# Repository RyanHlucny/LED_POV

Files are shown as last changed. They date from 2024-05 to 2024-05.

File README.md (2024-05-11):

# LED_POV

[NDSU](https://www.ndsu.edu/) Senior Design project: Two foot diameter LED spinning display using persistence-of-vision techniques.

## Documentation

The Documentation for this project is done using [GitHub Flavored Markdown (GFM)](https://github.github.com/gfm/) and [GitHub Pages](https://pages.github.com/). You can navigate around using the headers on the website. Many items are linked together, making for especially easy navigation.

## Software Development

If you are interested in setting up your software development environment similar to how I did in this project, I wrote a 'getting started' page for this. You can find that page at [Software Development](https://github.com/RyanHlucny/LED_POV/blob/main/SD403/Ryan%20Hlucny/Software%20Development/GettingStarted.md)

## Weekly Meetings

Our weekly meetings were where we got a lot of stuff done, and we took a lot of care and effort to document as much of the build process as we could. So please check out [Weekly Meetings](https://github.com/RyanHlucny/LED_POV/blob/main/SD403/Weekly%20Meetings/Weekly_Meetings.md) to see and learn more about this project.

## Media

Photos and videos from the project have been added to this [Google Photos Album](https://photos.app.goo.gl/s6BoLq5Lydn7EBvv7).

## THANK YOU

Got questions? [Contact us](https://github.com/RyanHlucny/LED_POV/blob/main/SD403/HW01/HW01_Contact_Information.md).

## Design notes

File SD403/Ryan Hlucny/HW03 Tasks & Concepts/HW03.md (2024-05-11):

# HW03 - Tasks & Concepts

## Ryan Hlucny

### Overview

- [Project Role](#project-role)
- [Tasks](#tasks)
- [Gantt Chart](#gantt-chart)
- [ECE Concepts](#ece-concepts)
- [ECE Tools](#ece-tools)

---

### Project Role

My role on the project is the Software and Controls lead. I will be overseeing the design of the software and controls for the project.

---

### Tasks

#### Task 1 - Image Transform & Processing

- Image pre-processing
- Pixel Transformation
- Brightness compensation
- Lag Compensation (to prevent "swirl" effect)
- ECE Concept: Image processing, Matlab

#### Task 2 - LED Control

- LED driver routine
- High-speed SPI communications
- ECE Concept: Embedded LED control

#### Task 3 - Interrupts

- Updating the LED command
- Reading sensor values
- ECE Concept: Embedded MCU Interrupts

#### Task 4 - State Space Model and Observer

- State Space model of system
- Observer design
- Angle estimation
- Latency Compensation?
- ECE Concept: Modern Control State Space modeling and Observing

---

### Gantt Chart

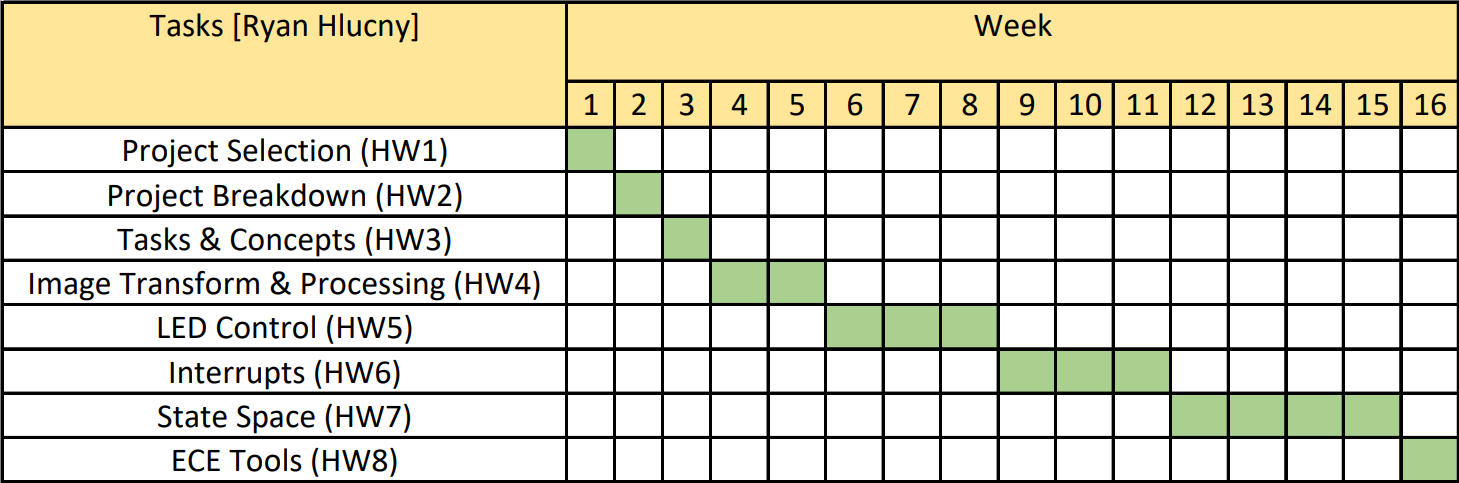
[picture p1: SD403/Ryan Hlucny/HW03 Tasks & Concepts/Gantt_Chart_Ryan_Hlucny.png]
Gantt Chart


---

### ECE Concepts

As listed in each of the above Tasks, my concepts are

- Concept 1 - Image Processing, Matlab
- Concept 2 - Embedded LED Control
- Concept 3 - Embedded MCU Interrupts
- Concept 4 - Modern Control State Space modeling and Observing

---

### ECE Tools

**Oscilloscope** - Measuring signal timing and signal characteristics. Debugging SPI communication channel between [Raspberry Pi Pico W](https://www.raspberrypi.com/documentation/microcontrollers/raspberry-pi-pico.html) and custom LED board utilizing [Adafruit DotStar (SK9822) Addressable RGB LEDs](https://www.adafruit.com/product/2343), and I2C Communications to [IMU sensor](https://www.sparkfun.com/products/15335).

**Development Environments** - I will be using [VS Code](https://code.visualstudio.com/) and the [Platform.io extension](https://platformio.org/) to develop the embedded code for the [Raspberry Pi Pico W](https://www.raspberrypi.com/documentation/microcontrollers/raspberry-pi-pico.html) in C++. I am running an [arduino-pico core](https://arduino-pico.readthedocs.io/en/latest/index.html), which ports the RP2040 mcu to the Arduino ecosystem, from [earlephilhower](https://github.com/earlephilhower/arduino-pico). The documentation for arduino-pico can be found [here](https://arduino-pico.readthedocs.io/en/latest/index.html).

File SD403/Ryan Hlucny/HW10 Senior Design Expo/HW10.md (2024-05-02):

# HW10 - Senior Design Expo

## Ryan Hlucny

### Favorite Project

My favorite project from the Senior Design Expo is the Head Tracker camera on the articulating/rotating platform using an IMU. I liked that it was interactive and it followed the sensor's movements really well. There were a lot of aspects to this project. Including wireless connectivity and a visualizer application. The ESP32 camera was also really cool! I could see uses for this in a deployable military/disaster recovery robot as a way for the operator to be able to clearly see around the robot while remotely controlling it. Very cool!

### Improvement

To improve the presentation, I would probably display a cut-section view of the rotation device to show off the internals and some diagrams to show the overview of the design. I would also like to see some kind of head/helmet mount for the sensor and have it battery powered so it doesn't have to be plugged in.

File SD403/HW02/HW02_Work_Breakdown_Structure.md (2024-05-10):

# Work Breakdown Structure - LED_POV

## SD_403_Sp24_06 LED Spinner

```mermaid
flowchart TB
  subgraph one [ ]
    L1(Level 1)
    A("
    Project 
    LED Spinning Display
    ")
  end
  subgraph two [ ]
    L2(Level 2)
    A --> B1("
    Ryan Hlucny
    Software/Controls
    ")
    A --> B2("
    Austin Houle
    Power Electronics
    ")
    A --> B3("
    Austin Kallhoff
    Mechanical/Hardware
    ")
  end
  subgraph three [ ]
    L3(Level 3)
    B1 --> C1(Major Activity)
    B1 --> C2(Major Activity)
    B2 --> C3(Major Activity)
    B2 --> C4(Major Activity)
    B3 --> C5(Major Activity)
    B3 --> C6(Major Activity)
  end
  subgraph four [ ]
    L4(Level 4)
    C1 --> T1(Task 1)
    C1 --> T2(Task 2)
    C2 --> T3(Task 3)
    C2 --> T4(Task 4)
    C3 --> T5(Task 1)
    C3 --> T6(Task 2)
    C4 --> T7(Task 3)
    C4 --> T8(Task 4)
    C5 --> T9(Task 1)
    C5 --> T10(Task 2)
    C6 --> T11(Task 3)
    C6 --> T12(Task 4)
  end
```

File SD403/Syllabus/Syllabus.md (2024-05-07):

# SD403 Syllabus

## SD_403_Sp24_06 LED Spinner

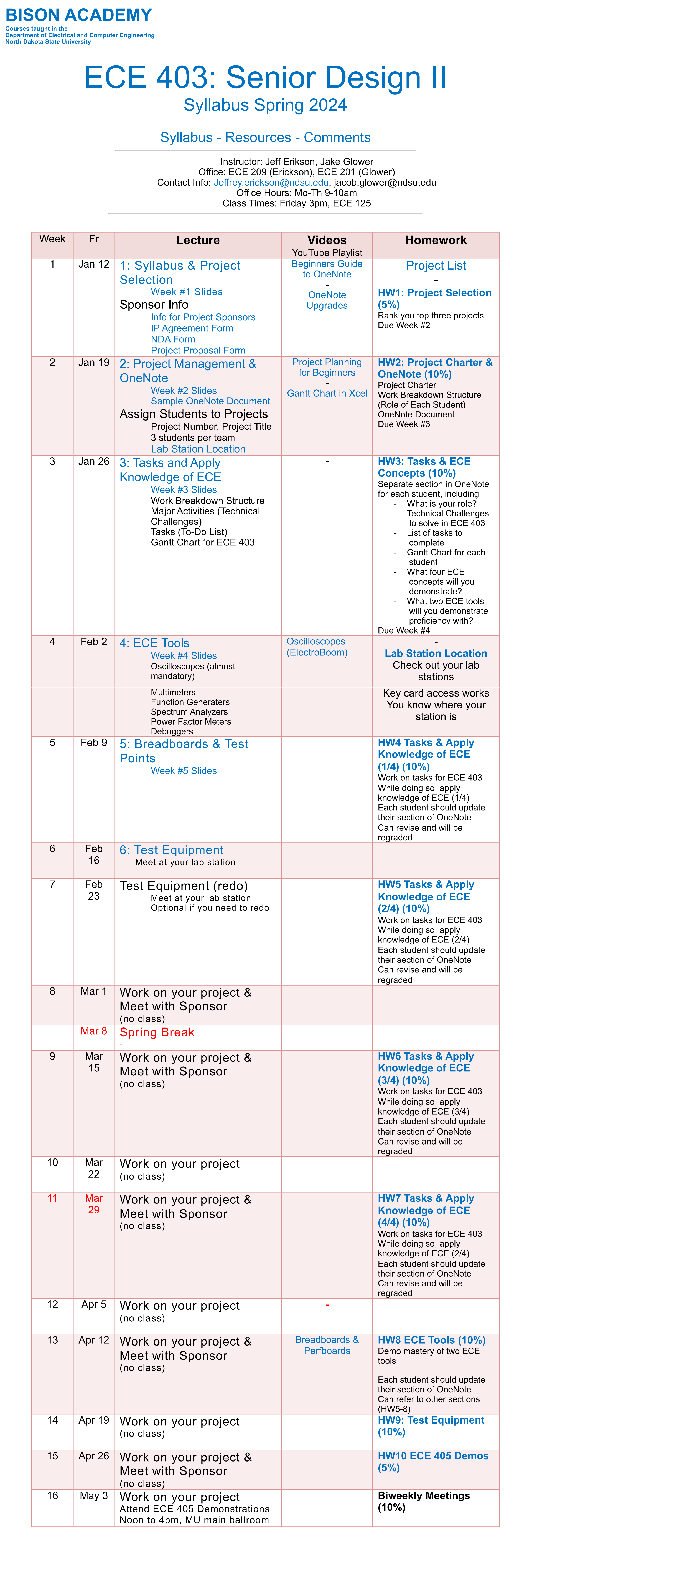
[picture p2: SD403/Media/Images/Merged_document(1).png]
Syllabus


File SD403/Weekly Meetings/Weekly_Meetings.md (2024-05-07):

# Weekly Meetings - LED_POV

## SD_403_Sp24_06 LED Spinner

This document shows our weekly meetings and progress throughout the semester.

### Overview

- [Feb 9, 2024](#feb-9-2024)
- [Feb 15, 2024](#feb-15-2024)
- [Feb 22, 2024](#feb-22-2024)
- [Feb 29, 2024](#feb-29-2024)
- [Mar 14, 2024](#mar-14-2024)
- [Mar 21, 2024](#mar-21-2024)
- [Mar 28, 2024](#mar-28-2024)
- [Apr 5, 2024](#apr-5-2024)
- [Apr 11, 2024](#apr-11-2024)
- [Apr 18, 2024](#apr-18-2024)

### Feb 9, 2024

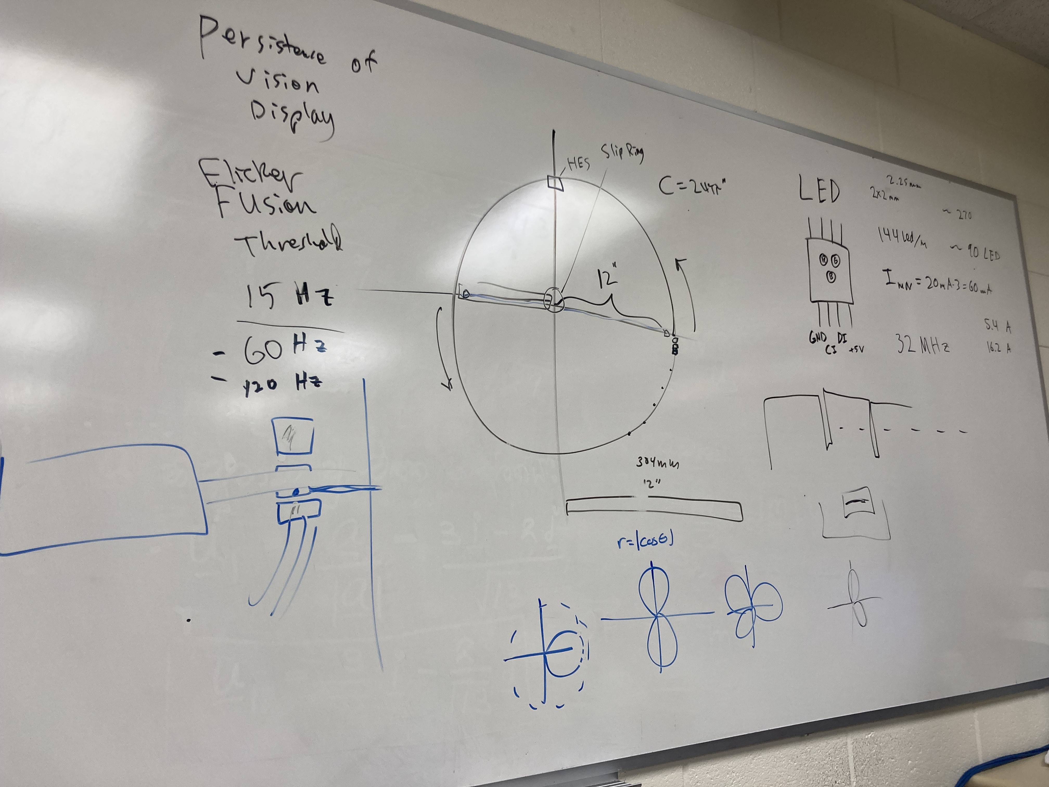
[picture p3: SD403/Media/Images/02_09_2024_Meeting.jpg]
feb-9-2024-meeting


### Feb 15, 2024

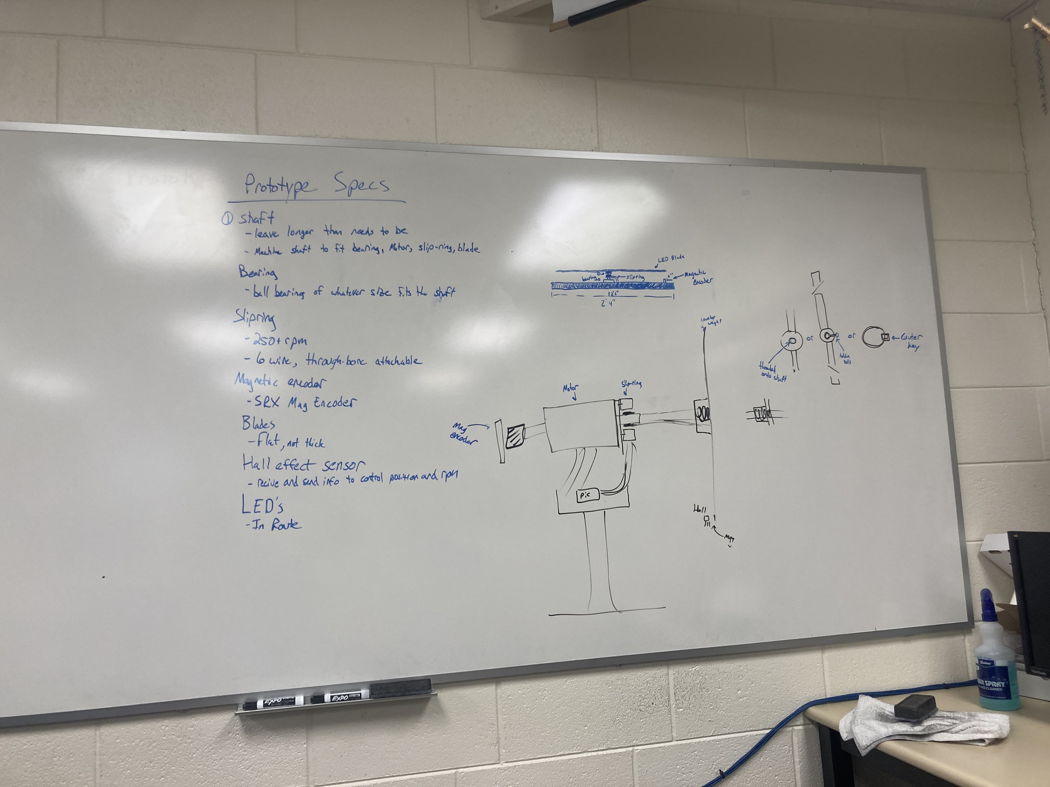
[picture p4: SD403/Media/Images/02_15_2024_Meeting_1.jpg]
feb-15-2024-meeting-1

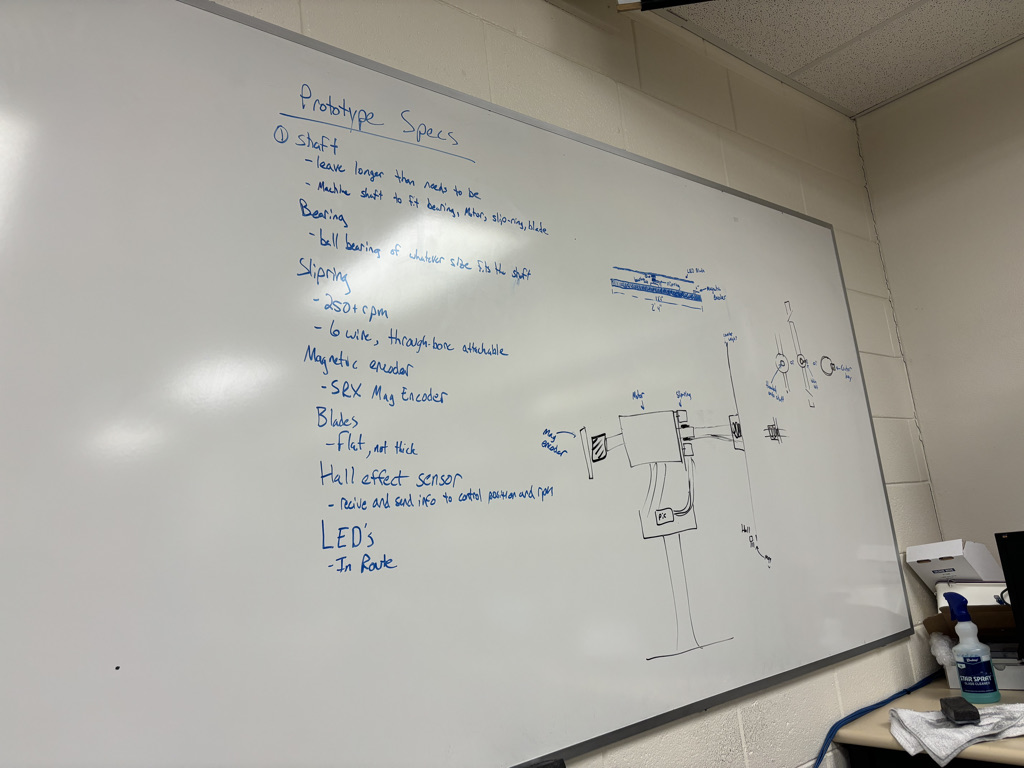
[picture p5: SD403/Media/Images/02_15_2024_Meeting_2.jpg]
feb-15-2024-meeting-2


### Feb 22, 2024

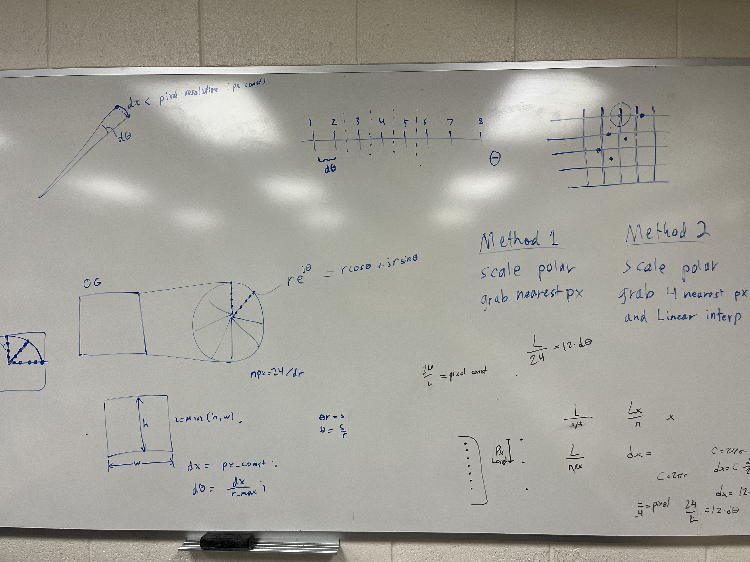
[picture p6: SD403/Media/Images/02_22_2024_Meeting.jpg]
feb-22-2024-meeting


https://github.com/RyanHlucny/LED_POV/assets/31110301/b2b64ef9-6dbf-48fa-892e-a6407bdd5961

MATLAB pixel transformation of a cartesian style pixel grid to polar style. This is necessary since the pixels will be spinning on the rotating platform. I will use the MATLAB program to generate a look-up-table (LUT) which will reduce the computational load for the Pico, and will only have to look-up pixel colors instead of performing the image transform itself. MATLAB is useful!

### Feb 29, 2024

No Pictures from our meeting this week.

### Mar 14, 2024

https://github.com/RyanHlucny/LED_POV/assets/31110301/247b1501-0b91-44f0-bc66-efd0bf0dff2f

### Mar 21, 2024

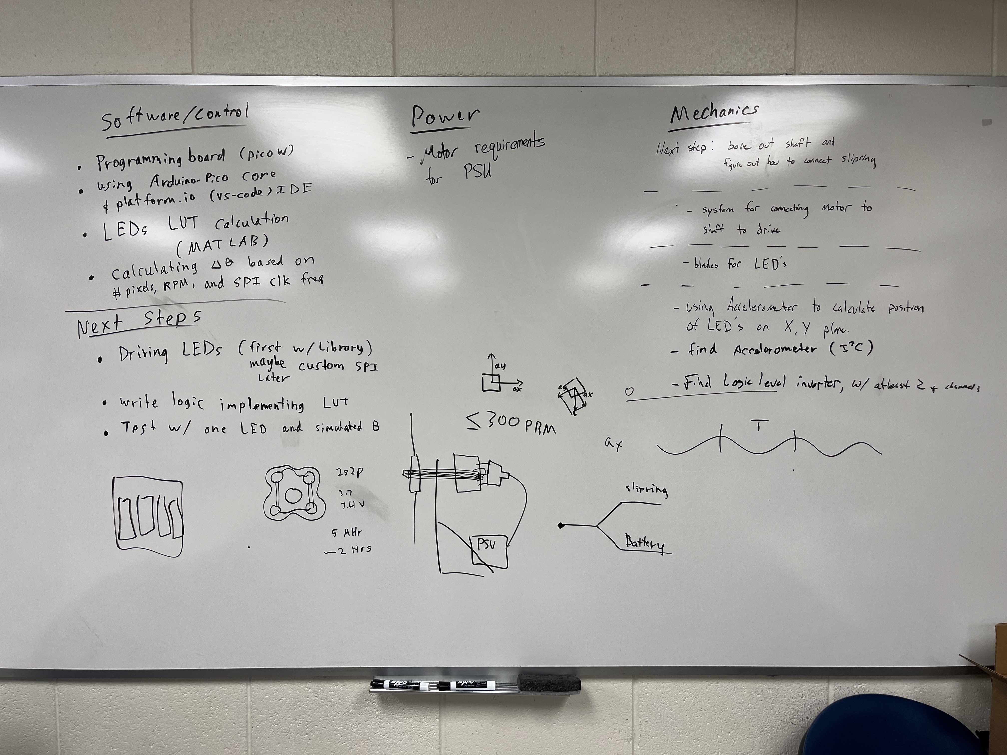
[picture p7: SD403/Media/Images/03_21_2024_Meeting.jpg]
mar-21-2024-meeting


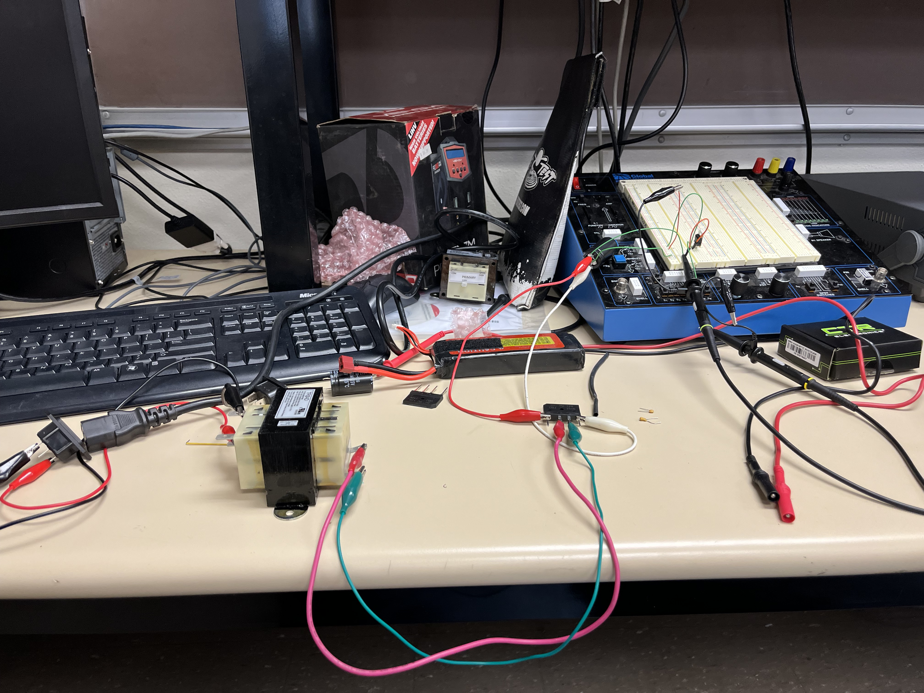
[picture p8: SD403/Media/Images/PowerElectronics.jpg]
power

Assembled Power electronics for the first time.

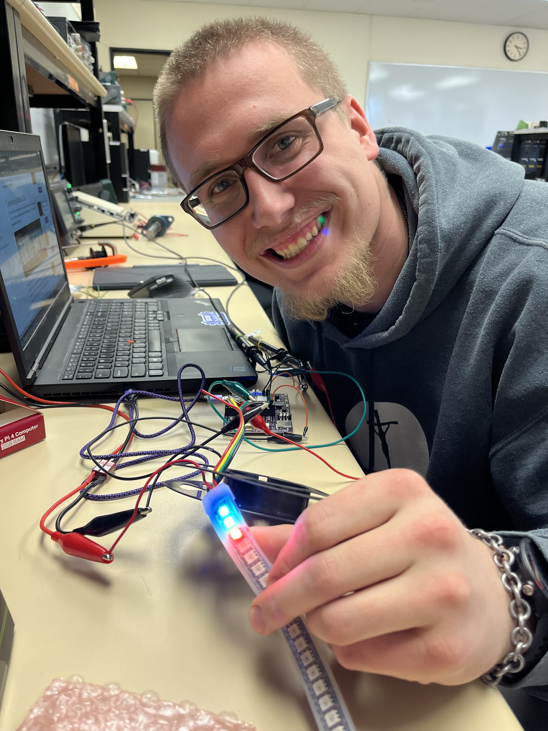
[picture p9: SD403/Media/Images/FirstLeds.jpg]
firstleds

First time getting Dotstar LEDs to run from our Raspberry Pi Pico W using arduino-core and Platform.io.

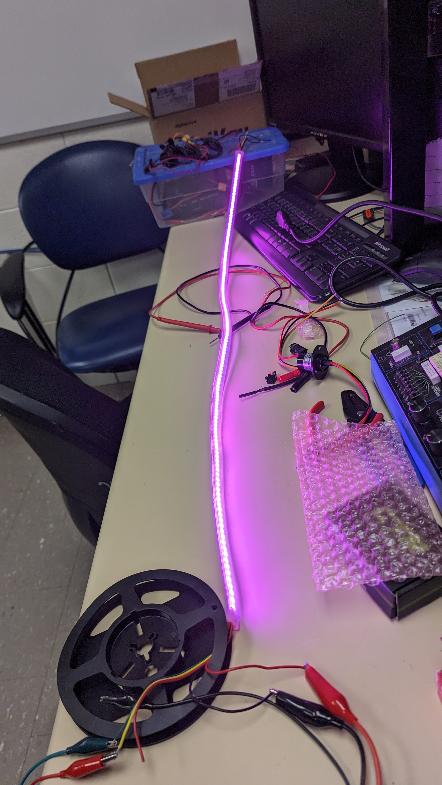
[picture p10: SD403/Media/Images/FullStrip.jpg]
fullStrip

Got the full strip to light solid while experimenting with SPI clock frequency. With this long of a strip (144 LEDs) we found the colors would start to fizzle out by the end of the strip if running too high of a frequency. Very stable at ~15 MHz, which is roughly half of the maximum frequency for the Dotstar LED chip.

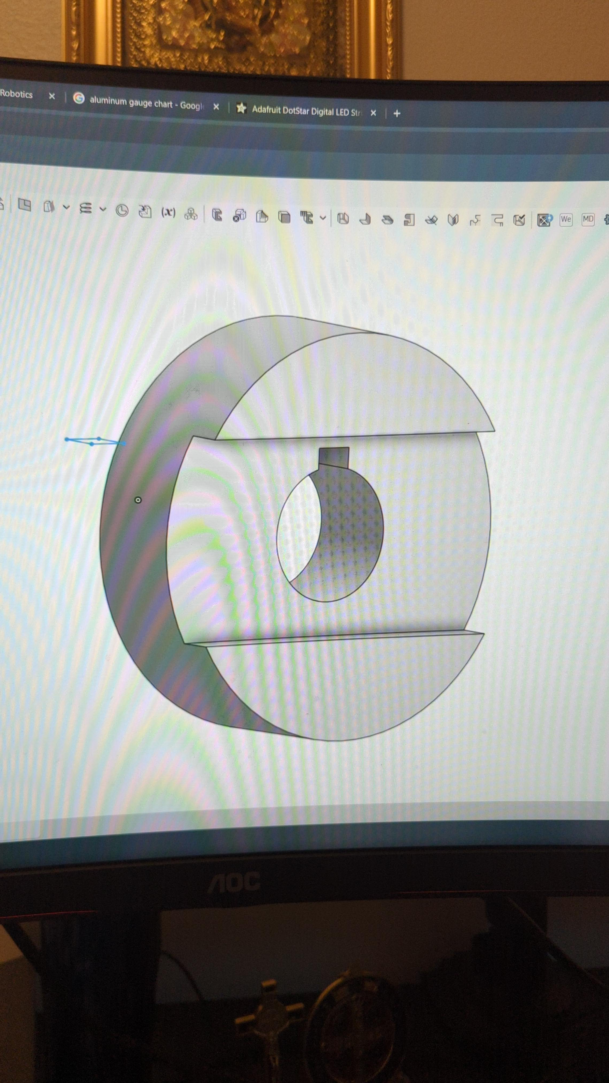
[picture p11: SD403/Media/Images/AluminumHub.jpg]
aluminumHub

CAD preview for the aluminum center hub.

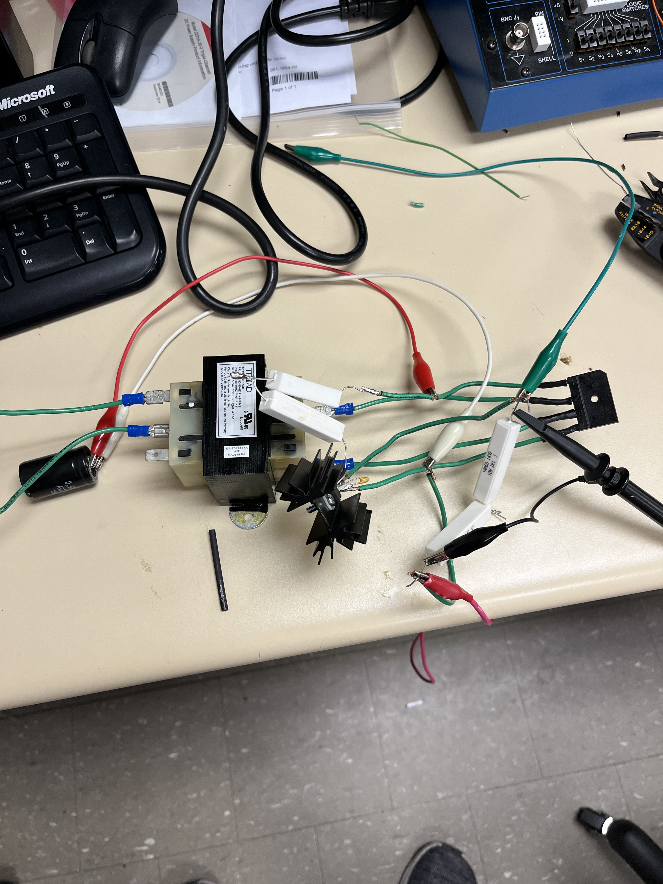
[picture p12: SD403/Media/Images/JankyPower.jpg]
jankyPower

Janky power setup for testing power supplies.

### Mar 28, 2024 Spring Break

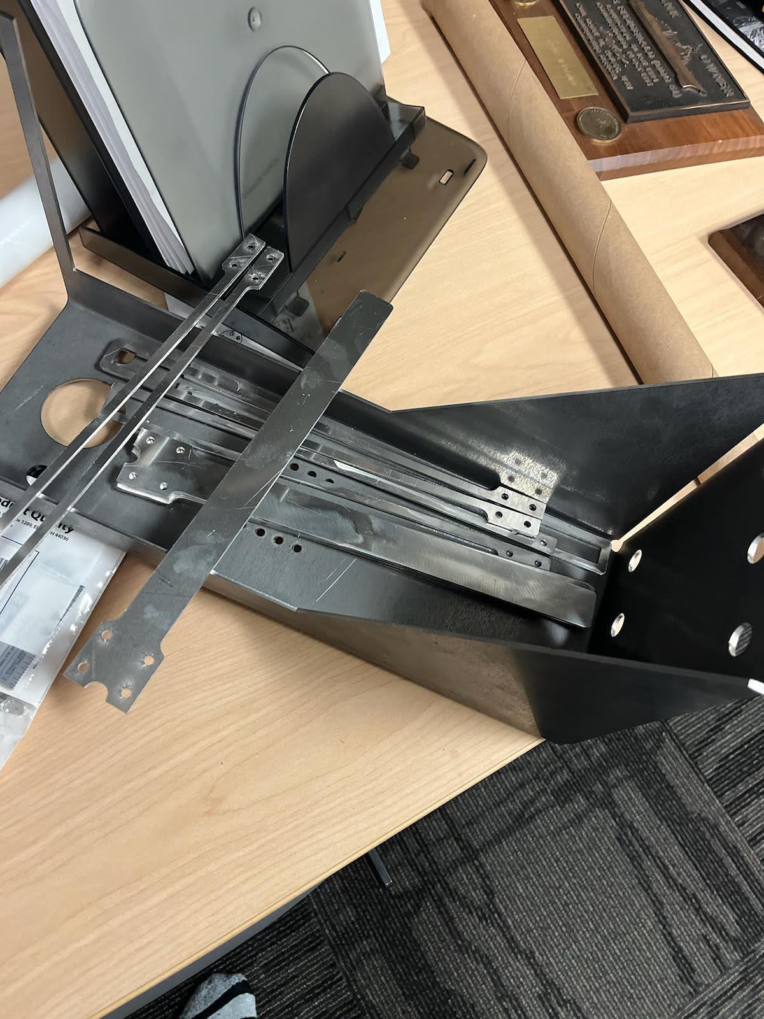
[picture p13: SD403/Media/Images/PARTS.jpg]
parts

PARTS!

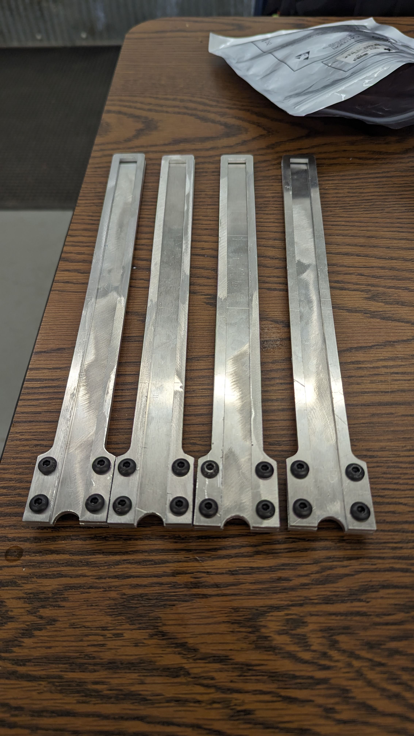
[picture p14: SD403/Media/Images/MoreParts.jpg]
moreParts

Assembling the blades.

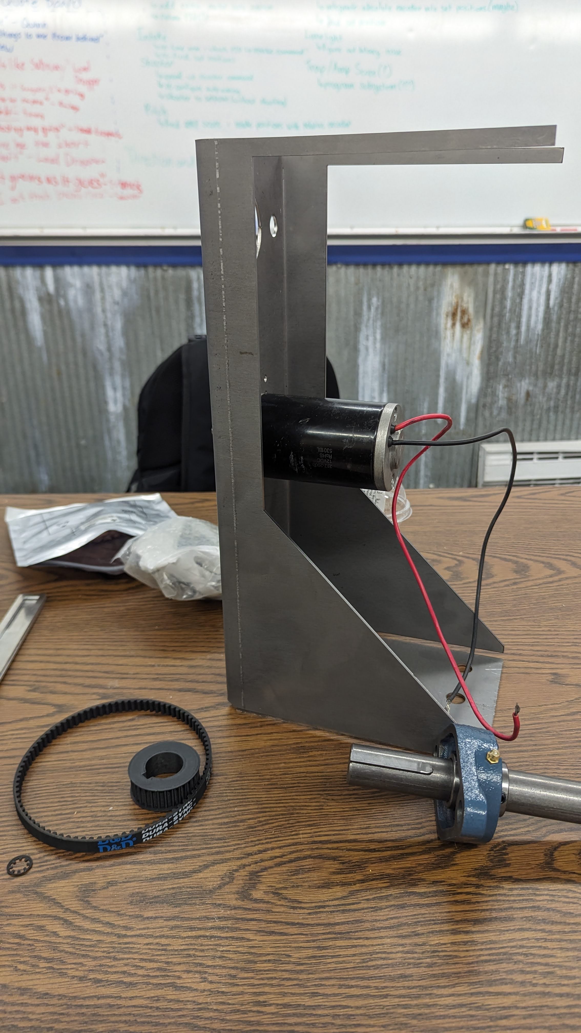
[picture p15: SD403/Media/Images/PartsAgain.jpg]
partsAgain

Attaching the DC motor to the frame with the 3D printed pulley.

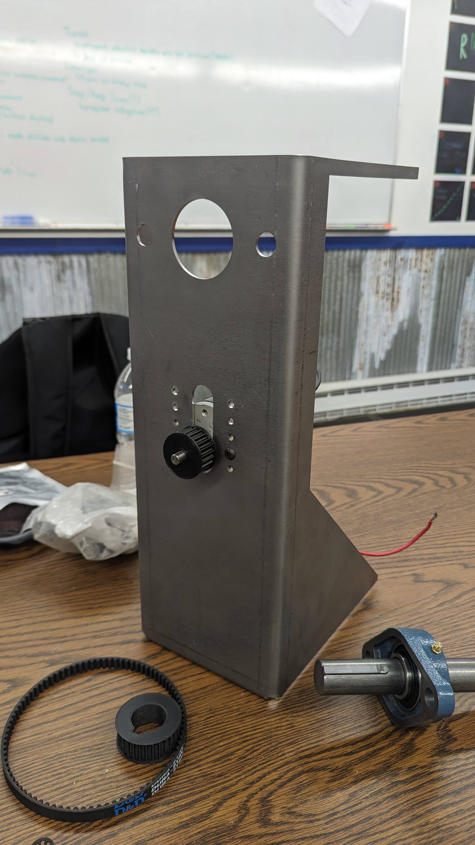
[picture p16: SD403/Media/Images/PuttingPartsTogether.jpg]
puttingPartsTogether

Front view.

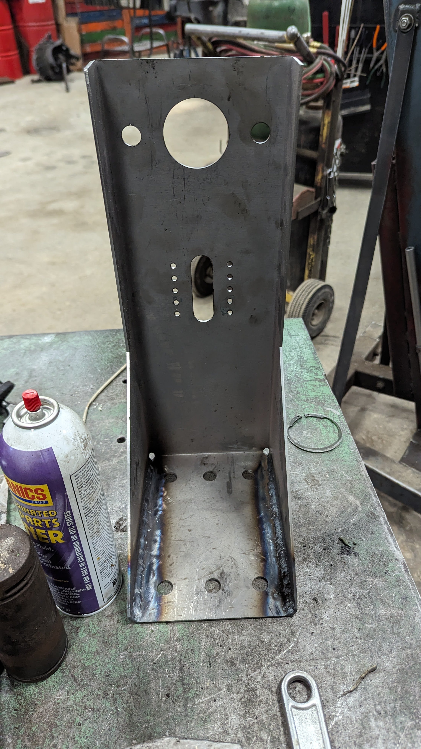
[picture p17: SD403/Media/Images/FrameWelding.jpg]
frameWelding

Welding the frame.

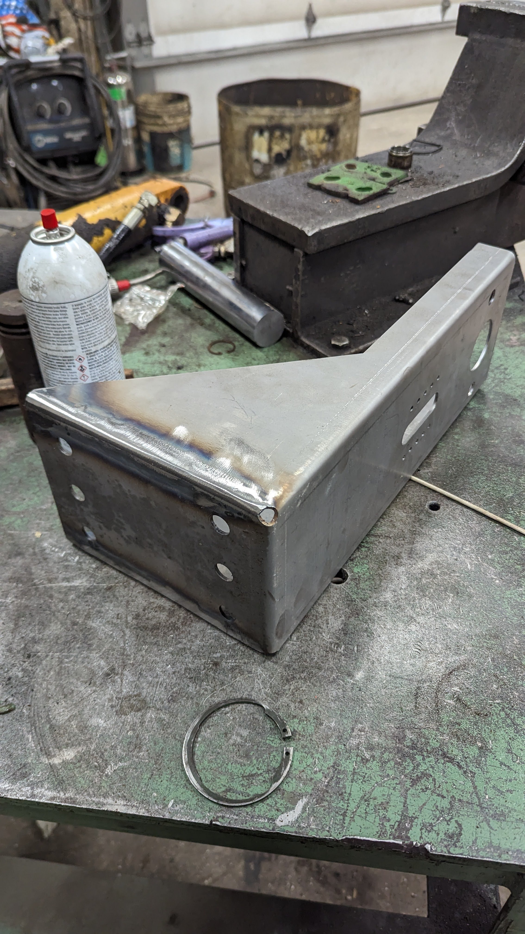
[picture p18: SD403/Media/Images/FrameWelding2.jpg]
frameWelding2

Cleaning up the welds.

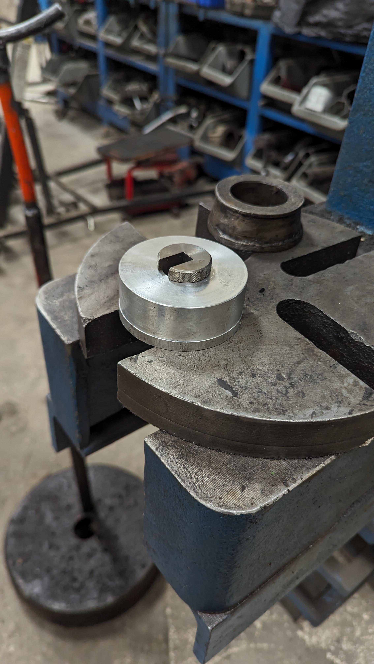
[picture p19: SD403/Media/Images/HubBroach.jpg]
hubBroach

Setting up to broach the keyway into the aluminum hub.

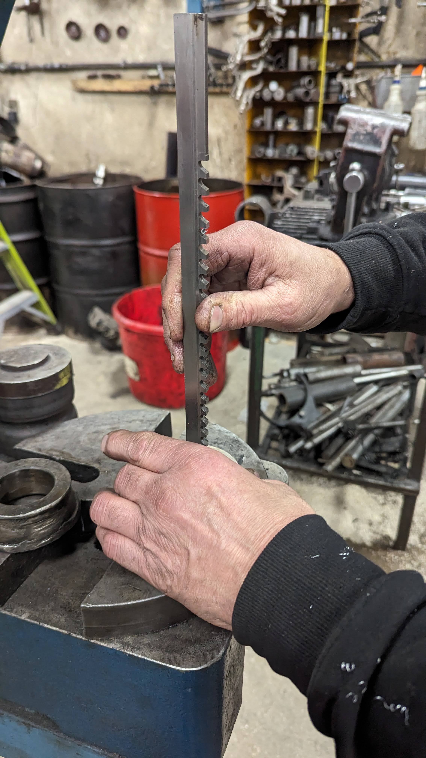
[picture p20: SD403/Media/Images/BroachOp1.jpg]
broachOp1

Broaching...

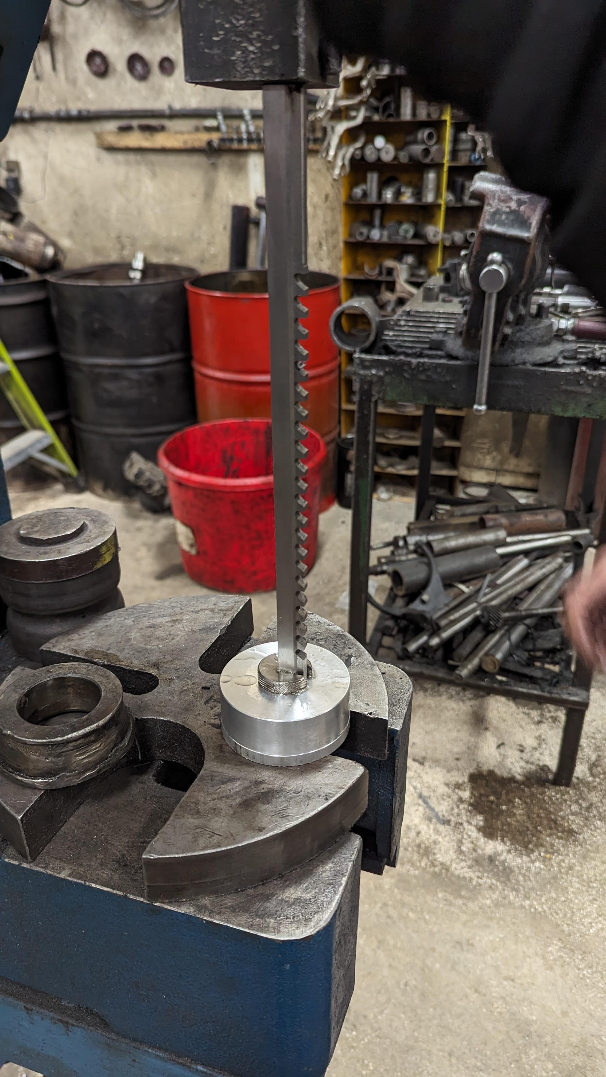
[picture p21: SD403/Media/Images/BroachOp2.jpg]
broachOp2


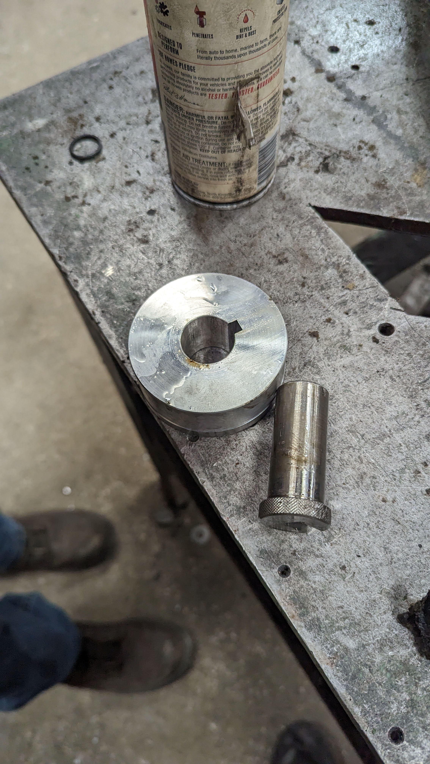
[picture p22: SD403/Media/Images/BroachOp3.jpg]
broachOp3


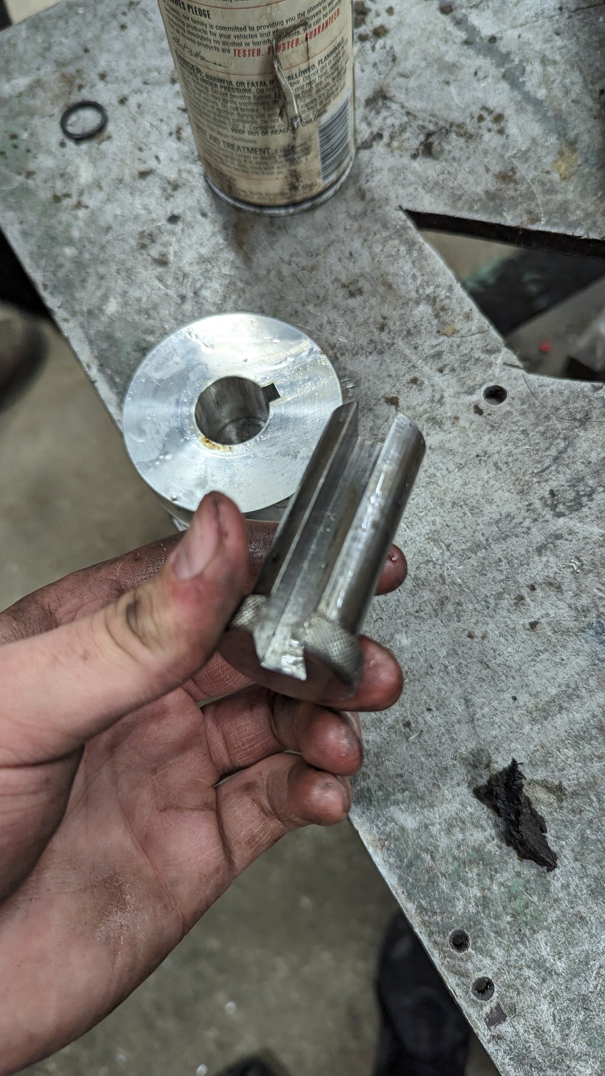
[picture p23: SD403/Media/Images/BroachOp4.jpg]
broachOp4


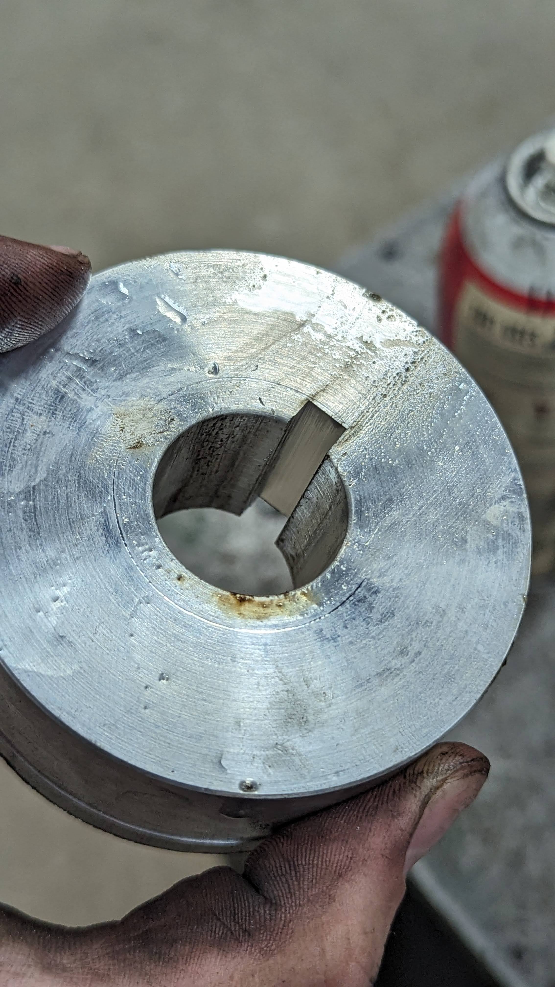
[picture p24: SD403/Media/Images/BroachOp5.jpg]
broachOp5

Finished product!

tigWelding
Janky tig welding setup for the blades. I added a second clamp on the side closer to the camera and the blades still buckled under all the heat from tig. Tig welding is hard!

welder
Miller Welder used.

millingChannel
Milling the channel.

https://github.com/RyanHlucny/LED_POV/assets/31110301/78458494-9d27-485f-92d1-7b921a663872

Milling operation video. This is done on a Bridgeport manual upright end mill.

fitmentTest
Fitting the blade in the channel

dualBladeFitmentTest
Blades fit nice!

bearings
Took us a while but realized the original bearing we were going to use was a self-aligning bearing. In other words, it would not hold up to any torques placed on the shaft. It's not meant to be used as a solo bearing solution - it requires another bearing to keep the shaft true. So we found these 1 inch ID steel ball bearings.

bearingBlock
So off to the races we went designing a new bearing block to hold the bearings. This design has a groove snapring to lock the bearings in.

bearingBlockNice
Printed with Matte Black Overture PLA (on a prusa i3 MK3S+) for prototype.

topCut
Here's a cut section of the "head" of the project, including the new bearing block.

electronicsCore
At the same time, we were designing the electronics core which would go on the other end of the shaft. The orange piece here is a mount for the IMU. The "cages" are for holding 21700 battery cells.

electronicsCorePrint
3D Printed.

### The Next Day

bearingBlockAssembled
Bearing block assembled with snapring to hold it together.

frameWithBearingBlock
Frame with bearing block mounted.

shaftWithKey
Shaft with Key and bore hole for wires to pass through to the LED blades.

fullASM
Full assembly (minus electronics).

cusectionTop
Cutsection of the top ASM

### Apr 5, 2024

apr-5-2024-meeting

### Apr 11, 2024

apr-11-2024-meeting-1
apr-11-2024-meeting-2
apr-11-2024-meeting-3
apr-11-2024-meeting-4
apr-11-2024-meeting-5

https://github.com/RyanHlucny/LED_POV/assets/31110301/fd784f13-caec-4af9-b8e1-2b49033294a1

First test running with the COTS slipring. All the electronics are spinning with the machine here, and it's getting power from a slip ring device.

### Apr 18, 2024

Apr-18-2024-meeting-1
Apr-18-2024-meeting-2

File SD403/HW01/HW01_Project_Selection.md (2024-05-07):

# HW01 Project Selection

## SD_403_Sp24_06 LED Spinner

### Project Selection

Project #14: **LED Spinner**

### Project Description

Design an LED spinning display than can produce an image and video production. Along with the LED display, design the PCB to power the project, as well as a stand to hold all apparatus'.

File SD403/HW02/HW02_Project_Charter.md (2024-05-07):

# Project Charter - LED_POV

## SD_403_Sp24_06 LED Spinner

### Deliverables

Design an LED spinning display than can produce an image and video production. Along with the LED display, design the motor to power the project, as well as a stand to hold all apparatus'

### Key Elements

Must Haves:

- Display Images
- Electric Motor
- Motor Controller
- Main controller (MCU)
- Stand
- AC Powered (Wall Outlet)

Nice to Have:

- Windows compatible Display
- Interactive Element for Display
- Detachable from stand
- Quiet (Low Air-Resistance)

### Time Allocated

2 Semesters

### Budget

$300 USD

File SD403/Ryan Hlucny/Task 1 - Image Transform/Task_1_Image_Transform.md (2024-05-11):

# HW04 - Task 1 - Image Transform

## Ryan Hlucny

### Task Overview

My first task includes creating a Look-up-table (LUT) which encodes the static image matrix data (pixel location and R, G, B values) into a new matrix which is indexed by a given angle $\theta$ and a radius $r$. This tasks includes the 4 following subtasks:

- Image pre-processing
- Pixel Transformation
- Twist Compensation (to counteract "swirl" effect)
- Brightness compensation

### Image pre-processing

Before I am able to use an image, it must first be converted into a usable file format. MATLAB has multiple different image colortypes (Indexed, truecolor, grayscale, etc). My matlab code is able to accept an image file which uses any of these color types. This is the relevant block of code which handles that:

```Matlab
%% Image importing
addpath("Images\");
imgpath = 'dahlia.jpg';
info = imfinfo(imgpath)
% Handle indexed and RGB images
if (info.ColorType == "indexed")
    % Indexed color type
    [A, Acmap] = imread(imgpath);
    A = ind2rgb(A, Acmap);
    A = uint8(A*255);
elseif(info.ColorType == "truecolor")
    % RGB color type
    A = imread(imgpath);
elseif(info.ColorType == 'grayscale')
    % Any other color type
    A = imread(imgpath);
    A = repmat(A,1,1,3);
end
```

I have imported a directory of images for testing, which is included in this Github Repository within this folder.

Then the image is (optionally) reduced and center square cropped so that there is no stretching on the original image when displayed on the LED Spinner. The relevant code is here:

```Matlab
figure(1); clf(1); subplot(311);
image(A); axis image; title('Original');
subplot(312);
dimsA = size(A); dimsA = dimsA(1:2);
reductionFactor = 1;
dimsB = round(dimsA/reductionFactor); 
B = imresize(A,dimsB);
image(B); axis image; title('Reduced');
subplot(313);
r = centerCropWindow2d(dimsB,[min(dimsB) min(dimsB)]);
C = imcrop(B,r); dimsC = size(C);
image(C); axis image; title('Center Square Crop');
rectangle('Position',[0 0 dimsC(1) dimsC(2)],'Curvature',[1 1]);

```

This code produces the following plots. Note that I am not reducing the image at all as the reduction factor is set to 1 in the code above.

ndsu-football-preprocessing

### Pixel Transformation

The general approach to the pixel transformation is shifting the origin from the corner of the image to the center and then constructing a new matrix $c(r,\theta)$ which returns a color vector of the form

```math
\begin{bmatrix} 
R\\ 
G\\ 
B 
\end{bmatrix}
```

which is our look-up-table.

The thing that makes this LUT useful is the fact that the microcontroller won't have to do any of these transformation calculations on-board, but all of it can be done before-hand in pre-processing.

Since LED placement is bound to be imperfect and we may have a different number of LEDs on each blade, I made the code capable of producing LUTs for setups with any number of LEDs on either blade and given an led spacing and starting offset from the center. These are constants we'll need to measure and determine on our device once it is fully assembled to produce the most accurate image.

The algorithm is implemented in Matlab as follows

```Matlab
%% Polar Plotting and LUT Construction
num_LEDs_right = 43; % 43
num_LEDs_left = 43; % 41
ledSpacing = 0.2734; % Distance from center to center of LEDs in inches
r_start_right = 0.05; % Distance from center of rotation to the first LED on right blade
r_start_left = r_start_right+ledSpacing/2; % Distance from center of rotation to the first LED on left blade
r_max_right = num_LEDs_right*ledSpacing;
r_max_left = num_LEDs_left*ledSpacing;
r = sort([r_start_right:ledSpacing:r_max_right, r_start_left:ledSpacing:r_max_left]);
% px_const = dr;
% dq = px_const/r_max; % Use this for "square-like spacing"
dq = 2*pi/275;
q = dq:dq:2*pi;

r_max = max(r_max_right,r_max_left)
scalex = dimsC(2)/r_max/2;
scaley = dimsC(1)/r_max/2;
h = dimsC(1); w = dimsC(2);

x = zeros(length(r),length(q));
y = zeros(length(r),length(q));
c = zeros(length(r),length(q),3);

figure(2); clf(2); tiledlayout('vertical');

% Variable parameters
% Represents a variable amount of 'twist' to predistort the image to help
% compensate for time lag in leds changing color. A value of 1 represents
% one full rotation at the outer ring of pixels. Set to 0 to disable
twist_const = 0.05;

[Q_twist,R] = meshgrid(q,r/r_max);
[m1,m2] = meshgrid(q,linspace(0,twist_const*2*pi,length(r)))
nexttile;
plot(R.*cos(Q_twist-m2),R.*sin(Q_twist-m2)); grid on; axis equal;
xlim([-1 1]); ylim([-1 1]); title("Twist Visualization");
subtitle(sprintf('Twist Factor = %f',twist_const));
% Represents the relative brightness of the center pixel compared
% to the pixels at the outer edge. Set to '1' to disable
relative_brightness_const = 0.75;

[Q,R] = meshgrid(q,r/r_max);
b = relative_brightness_const;
brightness_comp = (1-b)*sqrt((R.*cos(Q)).^2+(R.*sin(Q)).^2)+b;
% Plot brightness compensation surface (Z is the relative brightness)
nexttile;
surf(R.*cos(Q),R.*sin(Q),brightness_comp,'EdgeAlpha',0.25); axis equal; zlim([0,1]);
colorbar; colormap winter; title("Brightness Height Map");
subtitle(sprintf('Relative Brightness Compensation = %f',relative_brightness_const));

% Construction of LUT
idx = 0;
for j = 1:length(q), for i = 1:length(r)
    theta = -q(j)+pi/2;
    x(i,j) = r(i)*cos(theta); % inches
    y(i,j) = r(i)*sin(theta); % inches

    % Transforming from corner-origin cartesian coordinates to
    % centered polar coordinates
    x_transform = max(round(w/2+x(i,j)*scalex),1);
    y_transform = max(round(h/2-y(i,j)*scaley),1);
    
    % Produce a twist proportional to radius s/r = theta
    theta_twist = theta+twist_const*r(i)/r_max*2*pi;
    x_twist = r(i)*cos(theta_twist);
    y_twist = r(i)*sin(theta_twist);
    x_transform_twist = max(round(w/2+x_twist*scalex),1);
    y_transform_twist = max(round(h/2-y_twist*scaley),1);
    
    rgb = C(y_transform_twist,x_transform_twist,:);
    
    % Brightness Compensation
    c(i,j,:) = rgb * brightness_comp(i,j);

end, end
```

You may notice there are a couple additional compensation factors at play here. First is the twist compensation.

### Twist Compensation

When we drive the LEDs, we send a stack of color 'commands' to the LEDs, which is essentially a fancy sequence of bits describing the colors of all the LEDs in that strip. We will explore more about this in the next section, "Task 2 - LED Control". Each LED pops the top-most color command on the stack, removing it and using it for itself, and sends the rest of the command stack to the subsequent LEDs. Since it takes time for the controller to take in the data and pass it along, this process has an inherent time delay. Since the data sheet makes no mention of this time delay, we will have to determine this experimentally.

Due to the time delay, as the device spins, there will appear to be a "twist" or "swirl" effect in the image. This problem is exacerbated with higher rotation speeds, but it is there, to some degree, in all cases. This is because as the data propogates from one LED to the next, by the time each subsequent LED gets its command, the LED has already moved from where it was at the start of the command. Therefore, the LEDs will be off by some $\Delta\theta$, which is a function of rotational speed, radius, and time.

To compensate for the twist dynamically, it would require the microcontroller to recompute the LUT each time, which is not feasible. Therefore, we are generating a single LUT with a preset twist_const based on the expected rotation speed.

The twist compensation is implemented as a constant `twist_const`, which describes the number of turns the outer ring of pixels will turn from the default image. This constant can be negative or positive, which applies a "swirl" effect to the image. This can be thought of as a "pre-distortion" to the image to compensate for the natural swirl distortion which occurs in the image.

The Matlab script I wrote generates a twist visualization plot to visualize the twist being applied to the image.

twist_visual

### Brightness Compensation

Another factor that needs to be compensated is the brightness. As the device spins, at each $\Delta\theta$, the LEDs will get a new color command. The outer ring of LEDs are physically moving faster, which means the light from each LED is less concentrated in one spot in each $\Delta\theta$ interval.

Therefore a brightness compensation is required to equalize the brightness from the center of the image to the outside. The speed of each pixel is linearly proportional to radius, that is $$v \propto r$$ Hence the brightness compensation is implemented as a conical surface. The code above also displays a brightness height map visualization

brightness-map

The relative brightness compensation of 0.75 means the center pixels are 75% the brightness of the outside pixels.

The resulting image, after applying the twist and brightness compensation (compensation factors enlarged for the sake of viewing) would look like the following

https://github.com/RyanHlucny/LED_POV/assets/31110301/453112db-85e5-4b11-892b-0687b9dbed2b

### Summary

The Matlab code is included in this directory so you can take a look at it and play with it as you wish. The output of the program that will be used in the Pico microcontroller is the $c(r,\theta)$ matrix, which is a matrix describing the RGB color values of each pixel as an 8-bit integer.

#### ECE Concept: Image Transform (Image Processing / Analysis)

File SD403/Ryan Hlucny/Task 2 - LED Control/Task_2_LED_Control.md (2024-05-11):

# HW05 - Task 2 - LED Control

## Ryan Hlucny

### Task Overview

My second task includes controlling the LEDs. The Dotstar LED from Adafruit can be found [here](https://www.adafruit.com/product/2328#technical-details). The actual chip inside the "Dotstar" LED is the [SK9822](https://cdn-shop.adafruit.com/product-files/2343/SK9822_SHIJI.pdf).

The data sheet provides the data frame required to control the SK9822 using the [SPI](https://en.wikipedia.org/wiki/Serial_Peripheral_Interface) protocol. SPI stands for Serial Peripheral Interface, which is a simple communication protocol that includes a master and (multiple) slave device(s). The following diagram shows a basic overview.

```mermaid
  flowchart LR
    A(Master) -- MOSI --> B(Slave)
    B -- MISO --> A
    A --Data--> B
    A -- Clock--> B
```

`MOSI`: Master Out Slave In

`MISO`: Master In Slave Out

`Data`: Data line

`Clock`: Clock line

The Raspberry Pi Pico W has 2 dedicated hardware SPI busses. Each LED strip is going to have its own dedicated Hardware SPI bus.

```mermaid
  flowchart LR
    A(Pico W) -- SPI0 --> L1(LED Strip 0)
    A -- SPI1 --> L2(LED Strip 1) 
```

### Data Structure

#### Start Frame 32 Bits

| `0000 0000` | `0000 0000` | `0000 0000` | `0000 0000` |
| :---: | :---: | :---: | :---: |
| 8-bits | 8-bits | 8-bits | 8-bits |

#### LED Frame 32 Bits

| `111` | `Global` | `BLUE` | `GREEN` | `RED` |
| :---: | :---: | :---: | :---: | :---: |
| 3-bits | 5-bits | 8-bits | 8-bits | 8-bits |

#### End Frame 32 Bits

| `1111 1111` | `1111 1111` | `1111 1111` | `1111 1111` |
| :---: | :---: | :---: | :---: |
| 8-bits | 8-bits | 8-bits | 8-bits |

### Code

The SK9822 can be driven with a serial data frequency up to 30 MHz. However, at such high frequencies, we found the data signal fidelity would deteriorate as it propogates through the LED strip. It works fine at 30 MHz for ~10 LEDs, but with a longer strip the data signal is attennuated to the point that the color becomes corrupted. For a strip of 144 LEDs, I found that around 15 MHz worked well for signal fidelity and the signal made it to the end of the strip without any noticeable deterioration.

In order to use SPI communication techniques to communicate to the LEDs, you need to follow the above data structure. So I made a custom SPI LED library in C++ to accomplish this. It's a simple header and implementation file, which is included in the PlatformIO/LEDTest project in this repository. I will also include the source code at the bottom of this document.

The most important parts are the `SPI_LED::setStrip()` and `SPI_LED::write()` functions, which I will dive into now.

### `SPI_LED::setStrip()`

`pixelArray =`
| `led0` | `led1` | `led2` | ... |
| :---: | :---: | :---: | :---: |
| `[0  0  0]` | `[0  0  0]` | `[0  0  0]` | - - - |

Every **SPI_LED** object has its own `pixelArray` allocated in memory. This array is allocated to store all the RGB values for each pixel in the strip. The number of LEDs, the color ordering (RGB, BGR, GRB, etc), a pointer to the SPI interface object to use, as well as the SPI settings to configure the SPI for communication (frequency, data order, SPI mode), are all passed into the constructor and are initialized as private fields upon creation of an **SPI_LED** object.

`newPixelArray =`
| `led0` | `led1` | `led2` | `...` |
| :---: | :---: | :---: | :---: |
| `[255  0  0]` | `[0  255  0]` | `[0  0  255]` | `...` |

The `setStrip()` function takes in a new pixel array and copies the values into the **SPI_LED** object's `pixelArray` in memory. It does this by taking a pointer to the beginning of the new array and the size of that array in bytes, and then it uses the `std::copy` function built into the `std` library to copy the elements from the given array elements to the `pixelArray` pre-allocated at the creation of an **SPI_LED** object.

Performing `ledStrip.setStrip(&newPixelArray[0][0], sizeof(newPixelArray))` yields:

`pixelArray =`
| `led0` | `led1` | `led2` | `...` |
| :---: | :---: | :---: | :---: |
| `[255  0  0]` | `[0  255  0]` | `[0  0  255]` | `...` |

```c++
void SPI_LED::setStrip(uint8_t* newPixelArrayPtr, uint16_t size) {
    std::copy(newPixelArrayPtr, newPixelArrayPtr + size, this->pixelArrayPtr);
}
```

The elements must be copied to isolate the memory space of the **SPI_LED** `pixelArray` and to avoid memory corruption of the arrays.

Although it's not explicitly stated here, you can set partial arrays to only change a portion of the led strip. There is a variant of the `SPI_LED::setStrip` function which allows you to set a starting pixel index so you can set a desired region of pixels to the given pixel array.

### `SPI_LED::write()`

And finally the actual SPI communication. The code is fairly straightforward to read and is well commented, but essentially I am just following the datasheet on the protocol required to command these LEDs.

```c++
void SPI_LED::write() {
    if (!pixelArrayPtr)
        return;

    uint8_t *ptr = pixelArrayPtr, i;
    uint16_t n = numLEDs;

    spi->beginTransaction(spiSettings);

    // *** Start Frame ***
    for (i = 0; i < 4; i++)
        spi->transfer(0x00);
    
    // *** Pixel Data ***
    do {
        spi->transfer(0xFF); // Pixel start (setting global brightness frame to full)
        for (i = 0; i < 3; i++)
            spi->transfer(*ptr++); // Color Data
    } while (--n);

    // *** End Frame *** 
    // The number of bytes in the end frame is determined by the length of the strip,
    // Since its function is to allow the strip colors to propogate through the rest of the strip 
    for (i = 0; i < ((numLEDs + 15) / 16); i++)
        spi->transfer(0xFF);

    spi->endTransaction();
}
```

### Demo Code

The following code example shows how to use the library that I made, and will be followed with a video demo as well. In order to use the class, you just need to create an **SPI_LED** object with the number of LEDs, the color ordering, a pointer to the SPI interface object to use, as well as the SPI settings to configure the SPI for communication (frequency, data order, SPI mode). Since I will be using two strips and both SPI interfaces on the Pico W, I will have to create two **SPI_LED** objects in the final code for the project.

```c++
#include <Arduino.h>
#include "SPI_LED.h"
#include <SPI.h>

#define freq 1000000

SPI_LED ledStrip0(3, BGR, &SPI, SPISettings(freq, MSBFIRST, SPI_MODE0));
// SPI_LED ledStrip1(43, BGR, &SPI1, SPISettings(freq, MSBFIRST, SPI_MODE0));
uint8_t c1[3][3] = {{0, 0, 255},{0, 255, 0},{255, 0, 0}};
uint8_t c2[3][3] = {{0, 255, 0},{0, 0, 255},{0, 255, 0}};
uint8_t c4[2][3] = {{255, 0, 0}, {0, 0, 255}};

void setup() {   
    // Set up SPI0 with the proper pin assignments
    SPI.setSCK(PIN_SPI0_SCK);
    SPI.setTX(PIN_SPI0_MOSI);
    SPI.setRX(PIN_SPI0_MISO);
    SPI.setCS(PIN_SPI0_SS);

    ledStrip0.begin();
    ledStrip0.clear();
    ledStrip0.write();
}

void loop() {
    ledStrip0.setStrip(&c1[0][0], sizeof(c1));
    ledStrip0.write();
    delay(500);
    ledStrip0.setStrip(&c2[0][0], sizeof(c2));
    ledStrip0.write();
    delay(500);
    ledStrip0.setStrip(&c4[0][0], sizeof(c4),0);
    ledStrip0.write();
    delay(500);
    ledStrip0.setStrip(&c4[0][0], sizeof(c4),1);
    ledStrip0.write();
    delay(500);
    ledStrip0.clear();
    ledStrip0.write();
    delay(500);
}
```

The library also allows you to set individual pixel colors, using the `setPixelColor` function, but I have not demonstrated that since the functionality is quite simple and I won't be using it as it would be less efficient than using the `std::copy` function and doing the whole led strip at once. Nonetheless, below is a demo using that functionality anyways.

```c++
ledStrip0.setPixelColor(0,255,0,0);
ledStrip0.setPixelColor(1,0,255,0);
ledStrip0.setPixelColor(2,0,0,255);
ledStrip0.write();
```

### Results

Here is an image of the LEDs being controlled using my SPI library.

ledrgb

And here is a demo video of the above code.

https://github.com/RyanHlucny/LED_POV/assets/31110301/68bab8f0-ea38-421a-89dd-69bf47463b7b

### Summary

This SPI library will be integrated into the project as a whole. It has several feature which make it particularly nice for our application. More specifically, being able to set the entire `pixelArray` all at once is going to be useful for implementing the image pixel data LUT (Look-up-table) more efficiently.

#### ECE Concept: LED Control Embedded Systems

### Source Code

#### Source Code Header File "SPI_LED.h"

```c++
#pragma once

#include <Arduino.h>
#include <SPI.h>

// Color order flags. This depends on LED chips specification in its datasheet. 
#define RGB (0 | (1 << 2) | (2 << 4))
#define RBG (0 | (2 << 2) | (1 << 4))
#define GRB (1 | (0 << 2) | (2 << 4))
#define GBR (2 | (0 << 2) | (1 << 4))
#define BRG (1 | (2 << 2) | (0 << 4))
#define BGR (2 | (1 << 2) | (0 << 4))

class SPI_LED
{
    public: 
        SPI_LED(uint16_t numLEDs, uint8_t pixelType = BRG, SPIClass* spi = &SPI, SPISettings spiSettings = SPISettings(1000000, MSBFIRST, SPI_MODE0));
        void begin();
        void setPixelColor(uint16_t n, uint8_t r, uint8_t g, uint8_t b);
        void setStrip(uint8_t* newPixelArrayPtr, uint16_t size);
        void setStrip(uint8_t* newPixelArrayPtr, uint16_t size, uint16_t startPixel);
        void write();
        void clear();

    private:
        SPIClass* spi = NULL;
        SPISettings spiSettings;
        uint16_t numLEDs;
        uint32_t freq;
        uint8_t* pixelArrayPtr;
        uint8_t redOffset;
        uint8_t greenOffset;
        uint8_t blueOffset;
};
```

#### Source Code Implementation File "SPI_LED.cpp"

```c++
#include "SPI_LED.h"

/**
 * The SPI interface passed in must have the MOSI, MISO, clokc, and data lines set prior to construction of this object.
 * @param
*/

/**
 * @brief The SPI interface passed in must have the MOSI, MISO, clokc, and data lines set prior to construction of this object.
 * @param numLEDs the number of LEDs in the strip
 * @param freq the SPI clock frequency to be used
 * @param pixelType pixel color ordering
 * @param spi pointer to the hardware SPI class. (Must have ports defined prior to creation of this object)
 */
SPI_LED::SPI_LED(uint16_t numLEDs, uint8_t pixelType, SPIClass* spi, SPISettings spiSettings) : 
    numLEDs(numLEDs), freq(freq), pixelArrayPtr(NULL), redOffset(pixelType & 3), 
    greenOffset((pixelType >> 2) & 3), blueOffset((pixelType >> 4) & 3),
    spi(spi), spiSettings(spiSettings) { 

        free(pixelArrayPtr);
        uint16_t bytes = numLEDs * 3;
        if ((pixelArrayPtr = (uint8_t*)malloc(bytes))) {
            this->numLEDs = numLEDs;
            clear();
        } else {
            this->numLEDs = 0;
        }

    }

/**
 * @brief Begins the SPI interface passed in at the creation of this object
 */
void SPI_LED::begin() { spi -> begin(); }

/**
 * @brief Sets the color of a given pixel in the color array
 * @param n the pixel index (0 is the first led)
 * @param r Red value [0-255]
 * @param g Green value [0-255]
 * @param b Blue value [0-255]
 */
void SPI_LED::setPixelColor(uint16_t n, uint8_t r, uint8_t g, uint8_t b) {
    if (n < numLEDs) {
        pixelArrayPtr[n * 3 + redOffset] = r;
        pixelArrayPtr[n * 3 + greenOffset] = g;
        pixelArrayPtr[n * 3 + blueOffset] = b;
    }
}

/**
 * @brief Copies the values of a given array to the SPI_LED's pixelArrayPtr. 
 * Note that the color order (RGB, BRG, RBG, etc) in the array must match the pixelType this object was constructed with.
 * @param newPixelArrayPtr pointer to the first pixel of the new pixel array
 * @param size the length of the new pixel array in bytes
 */
void SPI_LED::setStrip(uint8_t* newPixelArrayPtr, uint16_t size) {
    std::copy(newPixelArrayPtr, newPixelArrayPtr + size, this->pixelArrayPtr);
}

/**
 * @brief Overload setStrup function which allows you to specify the starting pixel location to set only parts of a strip
 * @param newPixelArrayPtr pointer to thef irst pixel of the new pixel array
 * @param size the length of the new pixel array in bytes
 * @param startPixel the index of the first pixel to write (the first led index is 0)
 */
void SPI_LED::setStrip(uint8_t* newPixelArrayPtr, uint16_t size, uint16_t startPixel) {
    std::copy(newPixelArrayPtr, newPixelArrayPtr + size, this->pixelArrayPtr + startPixel * 3);
}

void SPI_LED::write() {
    if (!pixelArrayPtr)
        return;

    uint8_t *ptr = pixelArrayPtr, i;
    uint16_t n = numLEDs;

    spi->beginTransaction(spiSettings);

    // *** Start Frame ***
    for (i = 0; i < 4; i++)
        spi->transfer(0x00);
    
    // *** Pixel Data ***
    do {
        spi->transfer(0xFF); // Pixel start (setting global brightness frame to full)
        for (i = 0; i < 3; i++)
            spi->transfer(*ptr++); // Color Data
    } while (--n);

    // *** End Frame *** 
    // The number of bytes in the end frame is determined by the length of the strip,
    // Since its function is to allow the strip colors to propogate through the rest of the strip 
    for (i = 0; i < ((numLEDs + 15) / 16); i++)
        spi->transfer(0xFF);

    spi->endTransaction();
}

/**
 * @brief Sets the whole strip to off.
 */
void SPI_LED::clear() {
    memset(pixelArrayPtr, 0, numLEDs * 3); // 3 bytes/pixel
}
```

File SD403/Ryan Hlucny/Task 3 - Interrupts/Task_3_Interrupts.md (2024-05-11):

# HW06 - Task 3 - Interrupts

## Ryan Hlucny

### Task Overview

This project has specific timing requirements for it to work. Anytime when dealing with microcontrollers and precision timing is required, the solution is some kind of interrupt. In our case, I will be using timer interrupts to refresh the LED pixel color data buffer at a higher frequency than the microcontroller's main code loop runs. This will be necessary to get the maximum refresh rate possible and achieve persistence-of-vision.

### Timing

Persistence-of-vision is the phenomenon that allows a flickering object to appear static if the flickering occurs at a high enough frequency. This frequency is known as the **flicker-fusion threshold**. The flicker-fusion threshold is determined by many characteristics. The basic idea is that the flicker-fusion threshold needs to be high enough such that a receptor (our eyes) can no longer sense changes in an object. For our LED Spinner, multiple physical characteristics are changing all the time. Rotation angle $\theta$, angular velocity $\omega$, and the LED colors. Also, though imperceptibly fast, the red, green, and blue micro-LEDs within each LED flicker on and off really fast to achieve the desired color. This technique is known as PWM, and is being used to control the relative brightness of each micro-LED. For example, setting the RGB of a single led to,

| `Red` | `Green` | `Blue` |
| :---: | :---: | :---: |
| 127 | 0 | 255 |

yields a different duty cycle, or "on-time", for each micro-LED. With this color command, the red led has a duty cycle of ~50%, green 0%, and blue 100%.

So there are a lot of visible moving/changing features on the device. In order for persistence-of-vision to hold for a still image, we need all of these changing features to be above the flicker-fusion threshold. For the PWM of the LEDs, that's not an issue (otherwise you would see the flickering of the micro-LEDs while it's running). The greater challenge comes in making each "pixel" on the virtual "screen" appear constant. The challenging part with this is that because the LEDs themselves are spinning, they need to rotate $2\pi$ rad and update its pixel color faster than the flicker-fusion threshold. This is also challenging because the single LED strip needs to do this at every $\Delta\theta$ angle division as it rotates. So how fast does an LED strip need to update in order to achieve this? And how fast does the spinner need to spin?

### The Math

The flicker-fusion threshold for most human adults is 15 Hz, which is a surprisingly low number considering most of our computer screens and digital devices have screens have well above 60 Hz refresh rate. In our math, let's parameterize the refresh rate $f$, angle $\theta$, angular velocity $\omega$, and time $t$.

Assume $\omega=c$ to be constant (steady-state) for computing maximum operating conditions.

Then, $\theta(t) = \omega t$, and the equation of motion for an LED on the blade is $$r_i e^{j\theta(t)} = r_i e^{ j  \omega t}$$

where $r_i$ is the radius of the $i_{th}$ LED.

The refresh rate for a single LED (ie, the frequency of rotation, in Hz) is then $$f = \frac{\omega}{2\pi} = \frac{c}{2\pi}$$

So we simply need to pick $\omega$ such that $f$ is above the flicker-fusion threshold. However, there is another constraint. How fast can the microcontroller set the LEDs colors?

Each SPI transaction starts with a 32-bit start frame, followed by $n$ 32-bit LED frames, and ends with a 32-bit end frame. Thus the total number of bits to transfer in an SPI transaction is $$B = 64 + 32n$$ where n is the total number of LEDs in the strip. The SPI frequency $f_{SPI}$ is 1:1 with the bit rate, $T_b$, since SPI is a synchronous communication method where 1 bit is transfered each clock cycle. That is $T_b = f_{SPI}$. Which means the maximum transactions per second can be given by $$\frac{T_b}{B} = \frac{f_{SPI}}{B} \space\space\space transmissions/sec$$

Now there is going to be some amount of quantization error no matter what, because we are mapping rectilinear image pixels to a polar pixel space, and the polar space doesn't perfectly map to rectangular grid locations. The higher the resolution of the original rectangular image, the lower the quantization error. However, there may be additional quantization loss in making the LUT. The amount of space on a microcontroller is quite limited, so we can only store so much pixel data in the LUT. This is the motivation for limiting the resolution of the image. Only in a polar space, that limiting comes in the form of adjusting the number of angle divisions in the circle and the number of radius divisions along the radius. We denote the angle interval $\Delta\theta$, and the radius interval $\Delta r$. Fortunately, $\Delta r$ is constant and is exactly the distance between each subsequent LED, making our calculations simpler. However, $\Delta\theta$ changes based on $\omega$. For this reason, we will select $\Delta\theta$ to be some sufficiently small number associated with the normal operating conditions of the machine.

Now it would be useful to know the relationship between the SPI frqeuency, image resolution, and angular velocity of the machine. With $\Delta\theta$ intervals on the circle, that correlates to $$D = \frac{2\pi}{\Delta\theta} \space\space\space divisions$$ Each divion represents a whole new array of pixel information to read into each LED strip. Since each LED strip has its own independent SPI interface, we will only discuss one LED strip. This means the number of divisions is the number of transmissions required per rotation $T_r$: $$T_r = D = \frac{2\pi}{\Delta\theta} \space\space\space \frac{transmissions}{revolution}$$

This implies the number of "frames," or full revolutions, the microcontroller can drive in one second is

$$f = \frac{f_{SPI}}{BT_r} \space\space\space revolutions/sec$$

Hence the maximum frame rate that the microcontroller can drive, in terms of $f_{SPI},\space n, \space and \space \Delta\theta$ is $$f=\frac{f_{SPI}}{BT_r}=\frac{f_{SPI}}{B \left(\frac{2\pi}{\Delta\theta} \right)}=f_{SPI}\frac{\Delta\theta}{2\pi B }=f_{SPI}\frac{\Delta\theta}{2\pi \left(64+32n\right) }$$

The maximum SPI frequency I found to be reliable for a full strip was $f_{SPI} = 15.625$ MHz, and the number of LEDs per strip will be 53. Substituting these numbers and iterating on $f$ we get the following table:

| $f_{SPI}$ (MHz) | $n$ |  $f$ Hz  |  $\Delta\theta$ (rad)  |
| :---: | :---: | :---: | :---: |
|  15.625  |  53  |  5.0000  |  0.0035  |
|  15.625  |  53  |  10.0000  |  0.0071  |
|  15.625  |  53  |  15.0000  |  0.0106  |
|  15.625  |  53  |  20.0000  |  0.0142  |
|  15.625  |  53  |  25.0000  |  0.0177  |
|  15.625  |  53  |  30.0000  |  0.0212  |
|  15.625  |  53  |  35.0000  |  0.0248  |
|  15.625  |  53  |  40.0000  |  0.0283  |
|  15.625  |  53  |  45.0000  |  0.0318  |
|  15.625  |  53  |  50.0000  |  0.0354  |
|  15.625  |  53  |  55.0000  |  0.0389  |
|  15.625  |  53  |  60.0000  |  0.0425  |

Since the LUT is a static entity, we must select the $\Delta\theta$ in advance. Therefore, we choose $\Delta\Theta$ based on the desired refresh rate, $f$ that we want to see, and based on how much memory the Pico W has. The lower $f$ is, the smaller $\Delta\theta$, which results in a larger LUT (smaller $\Delta\theta$ implies more divions per rotation, which means more data stored in the LUT).

The LUT consists of a 3D array consisting of radius $r$ (led index) along the first dimension, angle $\theta$ along the second dimension, and the color data (blue, green, red) as unsigned 8-bit integers of type `uint8_t`. One 8-bit number is 1 byte. In our matrix, there would be $3n \left(\frac{2\pi}{\Delta\theta}\right)$ 8-bit integers; however, our device has 2 blades. We decided to offset the LEDs such that the two diametrically opposed blades interleave with each other. This effectively doubles the radius resolution. It also, however, doubles the size of our LUT. So, the LUT actually will have $n_2 = 2n$. So the size of the LUT is $$3n_2 \left(\frac{2\pi}{\Delta\theta}\right) = 3 \cdot 2n \left(\frac{2\pi}{\Delta\theta}\right) = 6n \left(\frac{2\pi}{\Delta\theta}\right) = \frac{12n\pi}{\Delta\theta} \space\space\space bytes$$

Using the values of $f$ and $\Delta\theta$ from the previous table, we have the following LUT sizes:

|  $\Delta\theta$ (rad)  |  LUT size (bytes)  |
| :---: | :---: |
|  0.0035  |  564631  |
|  0.0071  |  282316  |
|  0.0106  |  188211  |
|  0.0142  |  141158  |
|  0.0177  |  112927  |
|  0.0212  |  94106  |
|  0.0248  |  80662  |
|  0.0283  |  70579  |
|  0.0318  |  62737  |
|  0.0354  |  56464  |
|  0.0389  |  51331  |
|  0.0425  |  47053  |

The Pico W has a flash program memory of 2 MB, so any of these should fit. We will go with $\Delta\theta = 0.0035$ to give us the largest LUT we could need for the operating conditions we will see. With $f = 5$, the device will be spinning at 300 RPM (note that this is below the typical **flicker-fusion-threshold** for adults, though it would be fast enough for a proof-of-concept). which will be easily attainable by our hardware and is a good benchmark speed. Anything faster and it will start "skipping" $\Delta\theta$ steps, which is completely fine and will likely be unnoticeable.

### Interrupts

Now that we got all the preliminary calculations done, we need to set up interrupts to command the LEDs. The above calculations assumed that each LED command would follow immediately after the previous command (no dead-zone), which requires a specific frequency of sending SPI transmissions. I will call this transmission frequency $f_{transmission}$.

We calculated above the number of transmissions per second $$ f_{transmission} = \frac{f_{SPI}}{B} = \frac{f_{SPI}}{64+32n} \space\space\space transmissions/sec$$ In this context, $n = 53$, since each led strip has its own SPI interface. With $f_{SPI} = 15.625$ MHz, $$f_{transmission} = \frac{15.625 \cdot 10^6}{64+32\cdot53} \approx 8.878 \space kHz$$ This is the desired frequency of our interrupt to be able to send LED command SPI transmissions seamlessly, one to the next. So I will initialize my timer interrupt with a frequency of 8.878 kHz. This can be done as follows:

```c++
#include <Arduino.h>
#include <RPi_Pico_TimerInterrupt.h>

#define FLASH_TIMER_FREQ    8877.841

RPI_PICO_Timer timer0(0);

// Timer ISR
bool flash_led_callback(struct repeating_timer *t) {
    return true;
}

void setup() {

    Serial.begin(9600);
    pinMode(LED_BUILTIN, OUTPUT);

    timer0.attachInterrupt(FLASH_TIMER_FREQ, flash_led_callback);
}

void loop() {
    Serial.println("This is the main loop speaking...");
    delay(1000);
}
```

Using the RPI_PICO_TimerInterrupt library by Khoi Hoang.

Now it's time for the LUT implementation!

### Look-up-Table

The look-up-table is a giant array of uint8_t numbers in a particular order. This giant array of numbers is stored in flash program memory on the Pico. I implemented it as follows:

```c++
#include <stdint.h>

class LUT {
    
  public:
      static constexpr uint8_t flatimage[564450] = {
          53,51,12,50,50,11,66,120,118,33,116,132,31,116, ...
      }
}
```

Which is an array of 8-bit integers. There are over half a million integers in this array, so it's not really possible to display them all, but a few example LUTs has been generated and placed in my Task 1 folder. They simple have to be copy-and-pasted into the LUT file in the code, which I will include the source code just below here. You can also see the source code in the InterruptTest project in the PlatformIO folder in this repository.

After deploying the code to the Pico, we have the following memory statistics:

memoryusage

Which is awesome! We still have plenty of space left on the Pico for the rest of the program even after adding a massive LUT of image data. Here is a picture of the LUT.

LUT

Now enjoy this video of the comical scale of over half a million numbers...

[LUT Video](https://photos.app.goo.gl/fGBA41dUv3ot5QqcA)

### Summary

In summary, the timing on a device like this is critical for it to work properly. In fact, that is probably the only hard thing about this entire project: timing. With a time-critical application, we need to be smart with how we control it. Hardware interrupts are the best way to tackle any challenge with precise timing in embedded microcontroller programming. In the final project next semester, I will link the LUT up to the SPI_LED library which I made in Task 2, and use interrupts to perform the array switching, using SPI to transmit the data blazing fast! The last bit is knowing the angle of the device. This will be covered in my 4th task.

#### ECE Concept: Microcontroller Hardware Interrupts

### Source Code

```c++
#include <Arduino.h>
#include <RPi_Pico_TimerInterrupt.h>
#include <LUT.cpp>

#define FLASH_TIMER_FREQ    8877.841

RPI_PICO_Timer timer0(0);

// Timer ISR
bool flash_led_callback(struct repeating_timer *t) {
  // Add custom LED library calls here to change the LED data of the LED strips. 
  return true;
}

void setup() {
  Serial.begin(9600);
  pinMode(LED_BUILTIN, OUTPUT);

  timer0.attachInterrupt(FLASH_TIMER_FREQ, flash_led_callback);
}

void loop() {
  const uint8_t *p = &(LUT::flatimage[0]);
  Serial.println("B \t G \t R");
  // Print the color data for the first 10 LEDs
  for (int i = 0; i < 10; i++) {
      for (int j = 0; j < 3; j++) {
          Serial.print(*(p+3*i+j));
          Serial.print("\t");
      }
      Serial.println("");
  }
  delay(1000);
}

```

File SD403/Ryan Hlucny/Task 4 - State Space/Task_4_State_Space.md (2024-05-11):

# HW07 - Task 4 - State Space

## Ryan Hlucny

### Task Overview

The purpose of Task 4 is to create a state space model of the system in order to create an observer for the angle state of the system. This is going to then be used by the rest of the code to do the LUT indexing for LED array switching. The advantage of doing a state space model rather than merely euler integration techniques is the resulting estimate is much more accurate and gives us the benefit of sensor fusion. With sensor fusion, we can fuse multiple sensor sources together, taking the pros of each and leaving the cons. We are using an [ICM 20948](https://www.sparkfun.com/products/15335) as the IMU (inertial measurement unit) for this project. The imu is placed as centered as possible on the axis of rotation. From the IMU, we can get angle information from the gyroscope, but we can also get acceleration data from the accelerometer. Both of these sensors are integrated into the IMU, and we can access them independently. This will allow us to take both measurements into a sensor-fusion based observer using a C matrix with two outputs, one for each state. Additionally, this allows us to reject disturbances and noise a lot better from individal sensors. IF we know a particular reading is noisy, we can reduce its weight in a Kalman filter, giving us an "optimal" observer. Overall there are many benefits to the state space model, and it's also just really cool and fun to apply one of my favorite topics from school.

### The System

Here is a screen cap of my derivation of the state space system:

ss1

ss2

In my analysis I forewent the forces of friction and wind resistence. This is an innacuracy in my model and is definitely an area to improve/expand upon in the future.

Pluggin in the system into MATLAB, I was able to plot the response of the system to a unit step of torque.

```matlab
% SD_403_Sp24_06 LED Spinner
% Ryan Hlucny Task 4
% State Space Observer

addpath('.\ECE463_lib\');

m = 0.0453592; 
r = 0.3048; % 1 foot
 
A = [0 1; 0 0]
B = [0; 6/(m*r^2)]
C = [1 0; 0 1];
D = zeros(2,1);
eig(A)
G = ss(A,B,C,D)
```

I tried to pick values of m and r that were representative of our actual machine. I was surprised to see how sharp the response was. But it makes sense since the blades are so light and 1 Nm of torque is actually a lot for such a small mass. Coupled with the lack of friction and this response makes perfect sense.

state_Space_linear

We see that as time advances, the system evolves as we would expect. With no friction forces and a constant torque, the mass has a constant angular acceleration, which is why we see the curve in the plot of $\theta(t)$ and the staight line in $\omega(t)$. I turned the torque off after 0.25 seconds to simulate letting the device go into free-spin after a short period of acceleration. And we see here that the system decays into a constant $\omega(t)$ and linear $\theta(t)$, as expected.

### The Observer

The observer is designed using LQR techniques. I chose Q so that the angle state would have a much greater importance than the angular velocity state. This is because I am much more concerned with knowing the angle than I am its rate of change. The entire project is solely depending on the machine's ability to detect its angle state over time accurately.

#### Linear Simulation

```matlab
%% Observer Gains

Q = diag([1e4,1e2]);
R = 1;
H = lqr(A', C', Q, R)'

% Augmented system (Plant + Observer)
A4 = [A zeros(2,2); H*C (A-H*C)]
B4 = [B;B]
C4 = [1 0 0 0; 0 1 0 0; 0 0 1 0; 0 0 0 1];
D4 = zeros(4,1);
t = linspace(0,0.5,1e3);
X0 = [0;0;10*rand;10*rand];
U = ones(size(t)).*(t<0.25);
y = step3(A4, B4, C4, D4, t, X0, U);
figure(1); clf(1); set(gcf, "Name", "Linear Simulation");
tiledlayout('vertical'); nexttile;
plot(t,y(:,1)); grid on; title("\theta(t)"); nexttile;
plot(t,y(:,2)); grid on; title("\omega(t)"); 

figure(2); clf(2); set(gcf, "Name", "Linear Simulation with Observer");
tiledlayout('vertical'); nexttile;
plot(t,y(:,[1,3])); grid on; title("\theta(t)"); 
legend(["Plant", "Observer"]); nexttile;
plot(t,y(:,[2,4])); grid on; title("\omega(t)"); 
legend(["Plant", "Observer"]);
```

Running the above code yields a useful and important plot, showing the plant and observer states over time in this linear simulation. I gave the observer a randomly selected starting position to show that the observer tracks.

ssWithObserver

And the observer converges very quickly to the actual states.

#### Nonlinear Simulation

For the nonlinear simulation I wrote the dynamics equations into MATLAB and Euler integrated twice to get the system states. I am also animating the states while it's simulating to give a good visualization of what's happening with the system.

```matlab
%% Nonlinear Simulation

X = [0;0];
Xe = [rand;rand];
t = 0;
dt = 0.0005;
T = 1;
figure(3); clf(3); set(gcf, "Name", "Nonlinear Simulation");
q = X(1);
dq = X(2);
y = [];
while (t < 0.5)
  T = 1.*(t<0.25); % Only apply  torque for the first 0.1 seconds
  
  % Dynamics
  ddq = 6/(m*r^2)*T; 
  dq = dq + ddq*dt
  q = q + dq*dt;
  X(1) = q;
  X(2) = dq;

  % Observer dynamics
  dXe = H*C*X + (A-H*C)*Xe+B*T
  Xe = Xe + dXe*dt

  t = t + dt
  y = [y; X(1), X(2), Xe(1), Xe(2), T];

  % Animation
  plot([-r*cos(q), r*cos(q)],[-r*sin(q), r*sin(q)],'ro'); hold on;
  line([-r*cos(q), r*cos(q)],[-r*sin(q), r*sin(q)],"Color","r");
  plot([-r*cos(Xe(1)), r*cos(Xe(1))], [-r*sin(Xe(1)), r*sin(Xe(1))], 'go'); 
  line([-r*cos(Xe(1)), r*cos(Xe(1))],[-r*sin(Xe(1)), r*sin(Xe(1))],"Color","g"); hold off;
  grid on; axis equal; xlim([-1 1]); ylim([-1 1]); legend({'', 'Plant','','Observer'});
  pause(0.01)
end
hold off;
t = [1:length(y)]' * dt;
clf(3); tiledlayout('vertical'); nexttile;
plot(t,y(:,[1,3])); grid on; title('\theta(t)'); 
legend(["Plant","Observer"]); nexttile; 
plot(t,y(:,[2,4])); grid on; title('\omega(t)'); 
legend(["Plant","Observer"])
```

I also started the observer states in a randomly chosen position for this demo. This code yields the following video and plots of the simulation.

[Nonlinear Simulation (Google Photos)](https://photos.app.goo.gl/mzEL9quCqTYZ5SZXA)

And the plot,

stateSpaceNonlinearSim

### Summary

Eventually the State Space model and observer will be implemented in C++ using the Eigen library, and will be integrated with the SPI_LED library and the interrupt code with the Look-up-table. Having an accurate estimate of the angle state over time is critical to the correct operation of the machine.

#### ECE Concept: State Space LQR Observer

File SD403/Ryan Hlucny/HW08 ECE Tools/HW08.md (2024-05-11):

# HW08 - ECE Tools

## Ryan Hlucny

### Overview

I have had to use many ECE tools throughout the course of this project already. I will simply point out a few of the ECE tools I have demonstrated mastery of in my tasks.

### Tool 1 - MATLAB

I used MATLAB extensively in tasks 1, 3, and 4. In 1 I demonstrates skillful use of 3D plotting and 3D function generation. For task 3, I used MATLAB to generate the LUT which i tested in C++. And in task 4, all of the simulation and analysis for the state-space system was done using MATLAB, which required a certain level of mastery in and of itself.

MATLAB is one of the most powerful tools I've had the privilege of learning to use while studying my undergraduate degree at NDSU and while working at my internship with Collins Aerospace.

### Tool 2 - C++ Embedded Development in VS Code

In tasks 2 and 3 I developed a lot of code from scratch in C++ for the Pico W using the PlatformIO embedded development platform extension in VS Code. VS Code is another ECE tool which I have found to be of utmost importance. I use it at NDSU for my classes and I used it extensively while at my internship with Collins Aerospace. It is truly a versatile tool, similar to MATLAB, but it has its own perks and shortcomings. Pairing MATLAB and VS Code together makes a very strong combination of software and algorithm development and simulation abilities. Also just being able to have multiple projects open at the same time and working on a lot of different things at once can be challenging without being comfortable with a good IDE like VS Code.

### Tool 3 - Git

Probably the tool you never get to see me use is Git, and that's because I'm using it on the command line the whole time in the background while I'm developing code and documenting this project. Git is an *extremely* important ECE tool. Every internship I've been to had a huge component of git. And git was also one of the weaker areas of the engineers who were already there full-time. It's such a critical skill for developing any kind of ECE software in a team. It's the best way to version control your code or any type of project, really. And that's why I chose to use git to version control this project, including all my MATLAB, documentation, C++ programming in VS Code, LUT generation, images, videos, etc. All of it is version controlled by git. This is a very powerful way of working together in a team, or even solo just by having an easier way to manage and organize the project. This has also led me to the decision to host this project on GitHub, which is where all of the documentation for this project is located (which is where you're reading this right now... I know, crazy!) But really learning git is probably the best ECE tool I've learned and applied over and over again, from mentoring high-school robotics teams to working in the real world. It's used everywhere and I think it's one of the most worthwhile and powerful ECE tools you can learn.

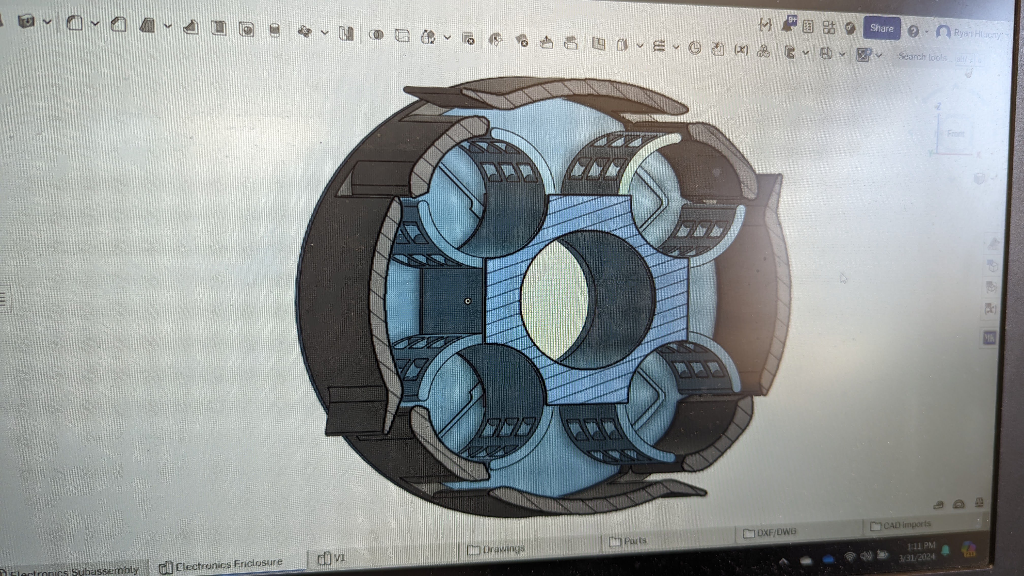
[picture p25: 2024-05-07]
SD403/Media/Images/ElectronicsEnclosurePrototype.jpg

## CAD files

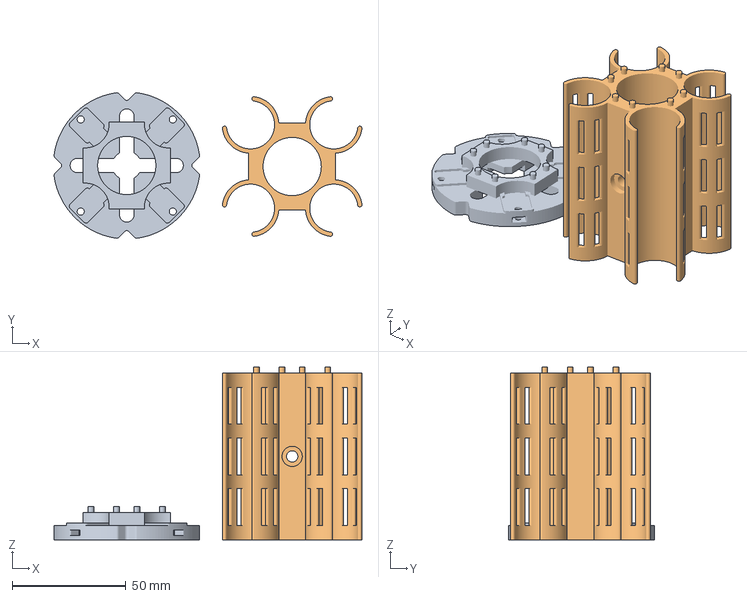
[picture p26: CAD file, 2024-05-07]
SD403/Ryan Hlucny/3D Printing/Electronics Enclosure - Core and Backplate only.3mf
135.2 x 63.9 x 75.8 mm
Electronics Enclosure - Back Plate (2).stl
Electronics Enclosure - Electronics Core (2).stl

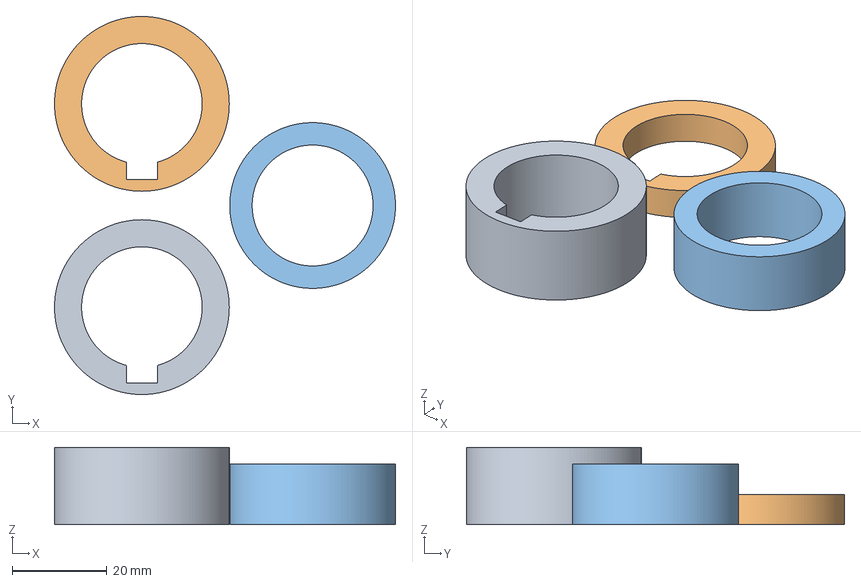
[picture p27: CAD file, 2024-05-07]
SD403/Ryan Hlucny/3D Printing/V1 - Spacers.3mf
71.9 x 79.7 x 16.2 mm
Main Pulley - Pulley Spacer.stl
Main Pulley - Hub Spacer.stl
V1 - Bearing Spacer.stl

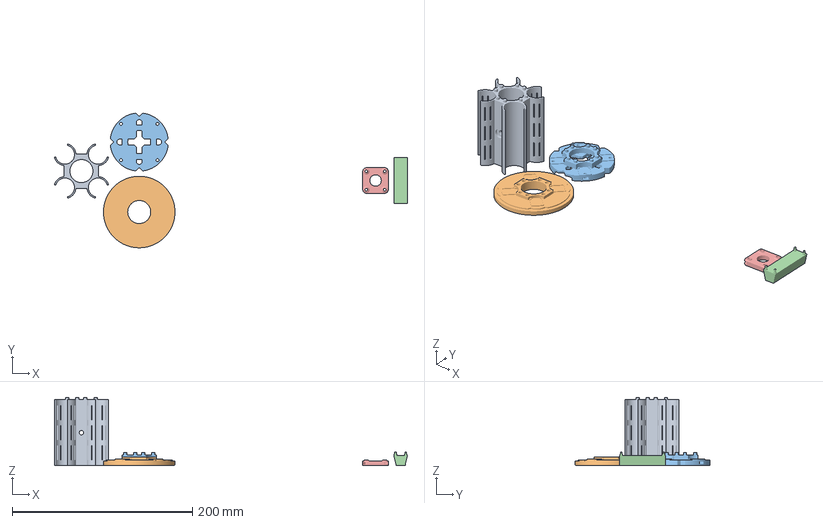
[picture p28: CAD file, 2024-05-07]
SD403/Ryan Hlucny/3D Printing/Electronics Enclosure interior.3mf
391.7 x 149.3 x 75.8 mm
Electronics Enclosure - Electronics Core (1).stl
Electronics Enclosure - Front Plate.stl
Electronics Enclosure - Back Plate (1).stl
Electronics Enclosure - Pico Mount.stl
Electronics Enclosure - IMU Mount.stl

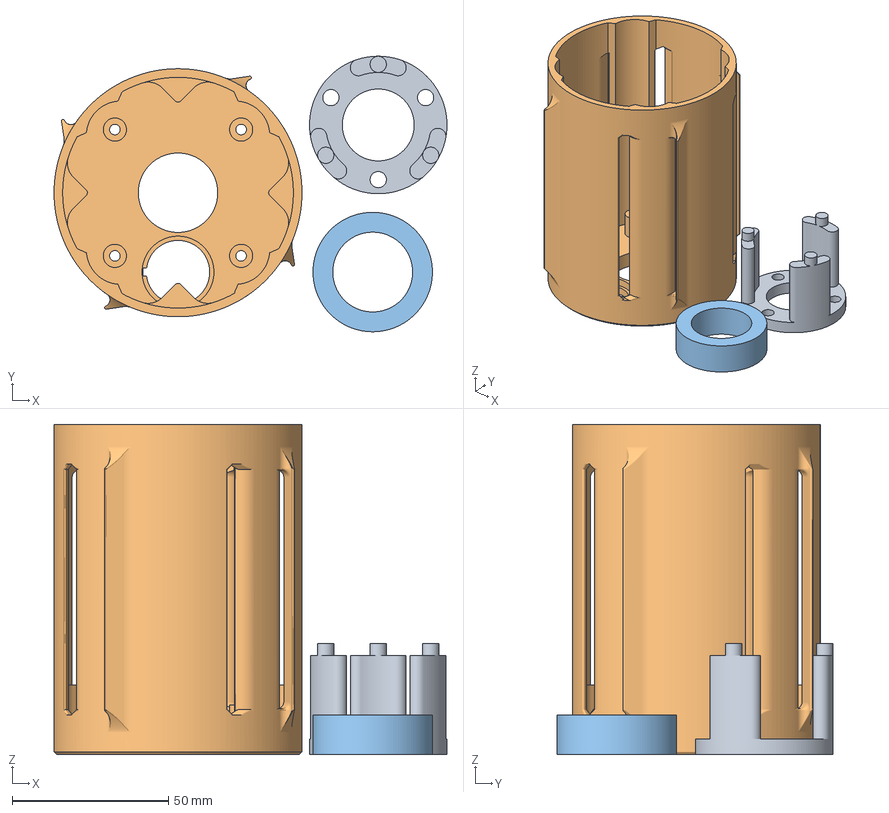
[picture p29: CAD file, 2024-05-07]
SD403/Ryan Hlucny/3D Printing/Electronics Enclosure exterior.3mf
125.8 x 88.2 x 105.7 mm
Electronics Enclosure - Slip Ring Mount.stl
Electronics Enclosure - Sleeve (2).stl
Electronics Enclosure - Electronics Spacer.stl

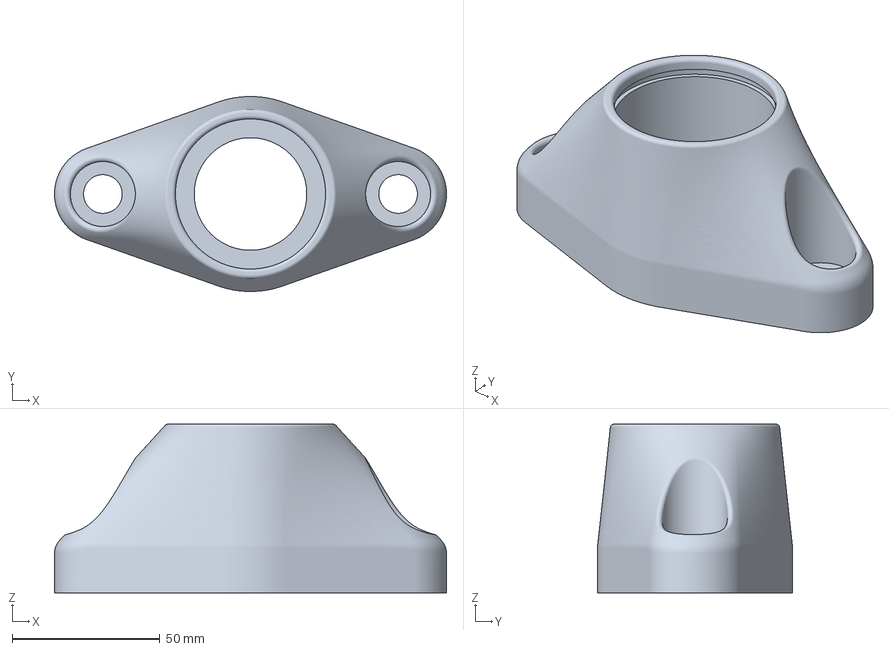
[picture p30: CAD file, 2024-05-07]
SD403/Ryan Hlucny/3D Printing/V1 - Bearing Housing.3mf
132.8 x 66.0 x 57.1 mm

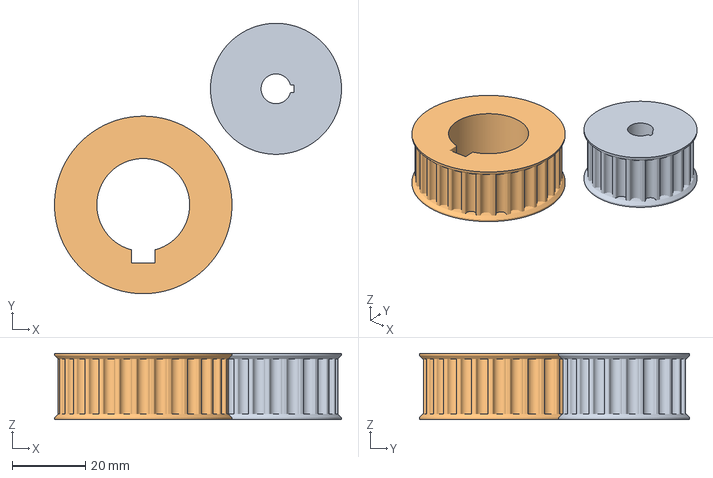
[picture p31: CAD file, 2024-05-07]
SD403/Ryan Hlucny/3D Printing/Pulleys.3mf
78.6 x 74.0 x 18.2 mm
Drive Pulley.stl
Main Pulley - Main Pulley.stl

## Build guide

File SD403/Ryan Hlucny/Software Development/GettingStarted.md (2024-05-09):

# Getting started with Raspberry Pi Pico W using Arduino-Pico core and Platform.io

## Ryan Hlucny

A major part of the software development for this project was done in VS code using the Platformio extension. Setting up a computer to allow you to develop code for a Raspberry Pi Pico W using the Arduino-core from Earle Philhower isn't trivial and I've had issues setting it up with Windows 10 and Windows 11. The purpose of this document is to streamline the process for anyone else wanting to set up their development environment in the same way as I did for this project.

### Arduino-Pico

Arduino-Pico is a port of the RP2040 microcontroller (the microcontroller of the Pico and Pico W) to the Arduino environment. This allows for easy software development for the Pico in Arduino code, which makes available to you many of the pre-existing libraries and hardware that are traditionally used with Arduino. This is relatively easy to set up and the installation steps can be followed [here](https://arduino-pico.readthedocs.io/en/latest/install.html). I haven't run into any snags getting Arduino-Pico set up on my Pico boards and uploading sketches to the board through the (new) Arduino IDE (I haven't tried the old one).

However, developing real software in the Arduino IDE leaves quite a bit to be desired, so I opted for an embedded development environment extension to VS Code called Platformio.

### PlatformIO

[PlatformIO](https://platformio.org/) is an embedded software development ecosystem, which is installed super easily as a VS Code extension (one-click installation!). PlatformIO boasts support for over 40 platforms, 20+ frameworks, over 1500 boards, and 13,000+ libraries. I first used PlatformIO as an upgraded alternative to the Arduino IDE (as I was already familiar with VS Code), and I grew to liking it for its ability to develop a lot more professional, industry standard software. It also makes expanding to other embedded platforms much easier. When starting this project I wondered if the Raspberry Pi Pico W can be programmed as an Arduino using the Arduino-Pico core, then could it also be supported by PlatformIO?

The answer is, **YES!**

This, however, is where the difficulties begin with setting up the development environment, since the Arduino-Pico core integration into PlatformIO is still a work-in-progress. I found it to be in a satisfactory state for this project. For instructions on PlatformIO integration follow [this](https://arduino-pico.readthedocs.io/en/latest/platformio.html) link. Make sure you follow all steps in that tutorial.

*NOTE: I was unable to enable long paths on my Windows 10 operating system, but PlatformIO integration has worked just fine.
Windows 11 worked just fine for me.*

Your `platformio.ini` file should look something like the following for a Raspberry Pi Pico W:

```ini
[env:rpipicow]
platform = https://github.com/maxgerhardt/platform-raspberrypi.git
board = rpipicow    
framework = arduino
board_build.core = earlephilhower

```

(*Note* that this file will be different for a Raspberry Pi Pico and a Raspberry Pi Pico W)

### Windows Drivers

*__Warning:__ I had to perform the below steps for my both my Windows 11 and Windows 10 PC.*

Additionally, if you have troubles with uploading code to your Pico W, you may need to install the correct drivers for the Pico W device. You can find the solution to this problem [here](https://github.com/earlephilhower/arduino-pico/discussions/1591).

Install Zadig and you should be able to install the correct drivers found at the link above relatively easily. Then you should be able to upload code to your Pico W using Arduino-Pico core with VS Code and the PlatformIO development environment.

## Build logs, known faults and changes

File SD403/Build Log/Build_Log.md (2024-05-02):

# Build Log - LED_POV

## SD_403_Sp24_06

This document shows our weekly meetings and progress throughout the semester.

### Overview

- [Feb 9, 2024](#feb-9-2024)
- [Feb 15, 2024](#feb-15-2024)
- [Feb 22, 2024](#feb-22-2024)
- [Feb 29, 2024](#feb-29-2024)
- [Mar 21, 2024](#mar-21-2024)
- [Apr 5, 2024](#apr-5-2024)
- [Apr 11, 2024](#apr-11-2024)
- [Apr 18, 2024](#apr-18-2024)

### Feb 9, 2024

feb-9-2024-meeting

### Feb 15, 2024

feb-15-2024-meeting-1
feb-15-2024-meeting-2

### Feb 22, 2024

feb-22-2024-meeting

### Feb 29, 2024

<!-- ![feb-29-2024-meeting](.\images\02_29_2024_Meeting.jpg) -->

### Mar 21, 2024

mar-21-2024-meeting

### Apr 5, 2024

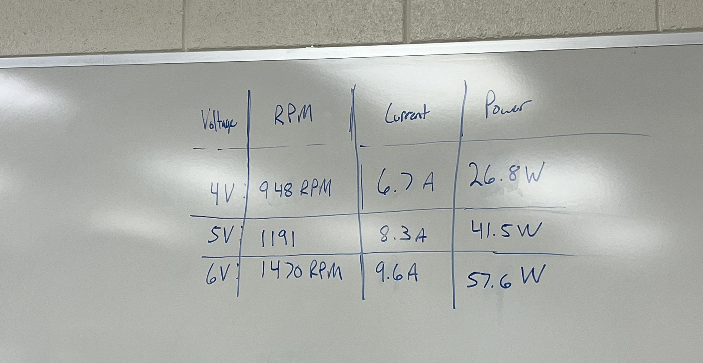
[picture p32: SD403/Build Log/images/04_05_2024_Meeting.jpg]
apr-5-2024-meeting


### Apr 11, 2024

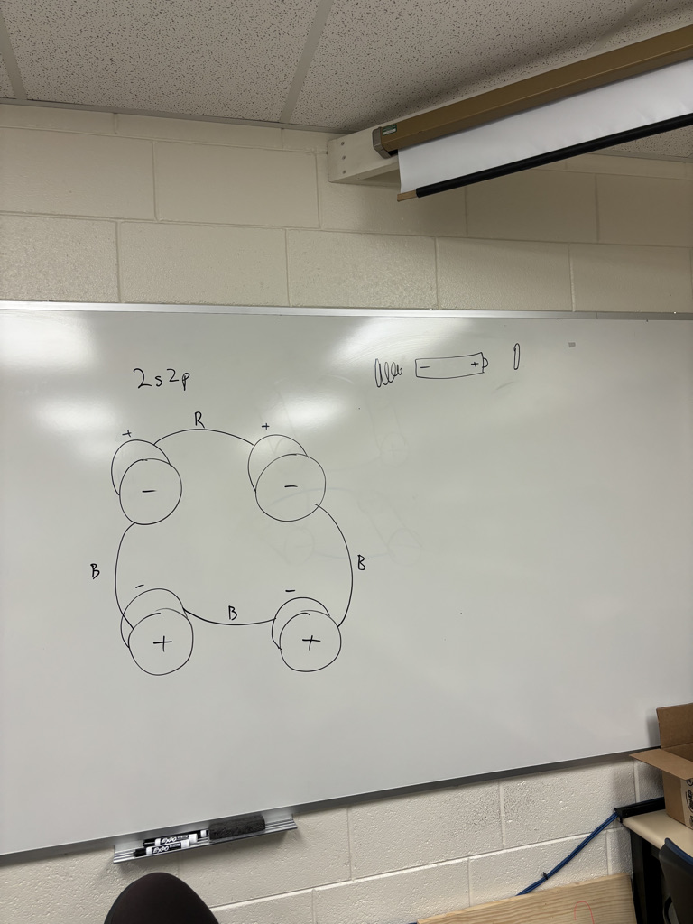
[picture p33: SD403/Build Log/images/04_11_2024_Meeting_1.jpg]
apr-11-2024-meeting-1

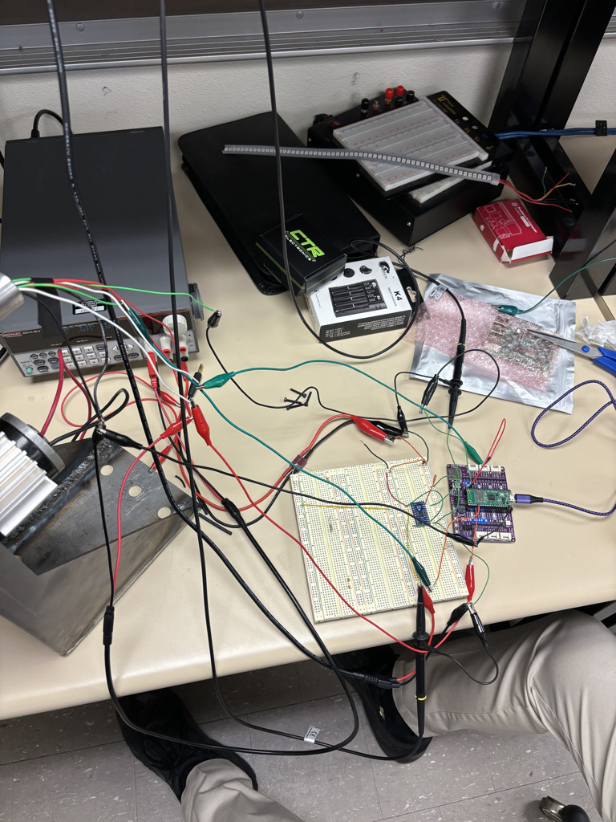
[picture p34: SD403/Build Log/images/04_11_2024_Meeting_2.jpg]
apr-11-2024-meeting-2

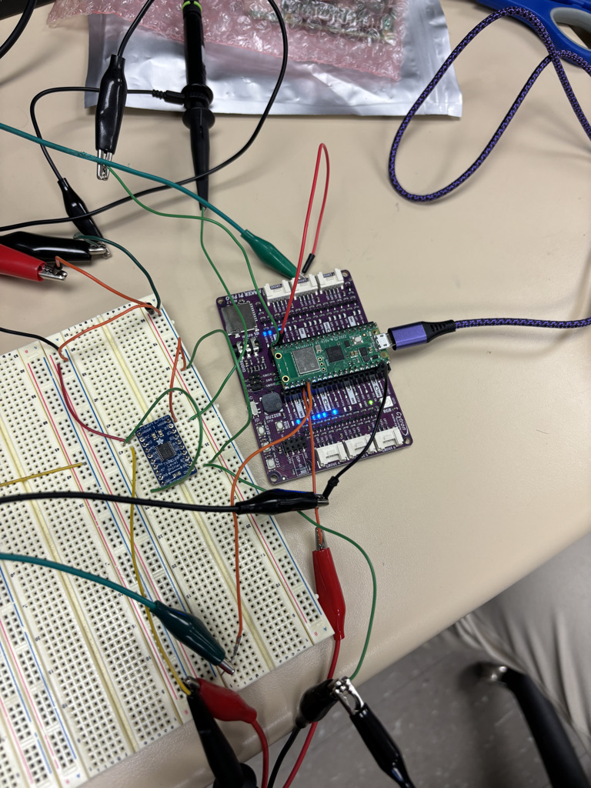
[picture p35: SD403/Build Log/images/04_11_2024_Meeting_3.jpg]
apr-11-2024-meeting-3

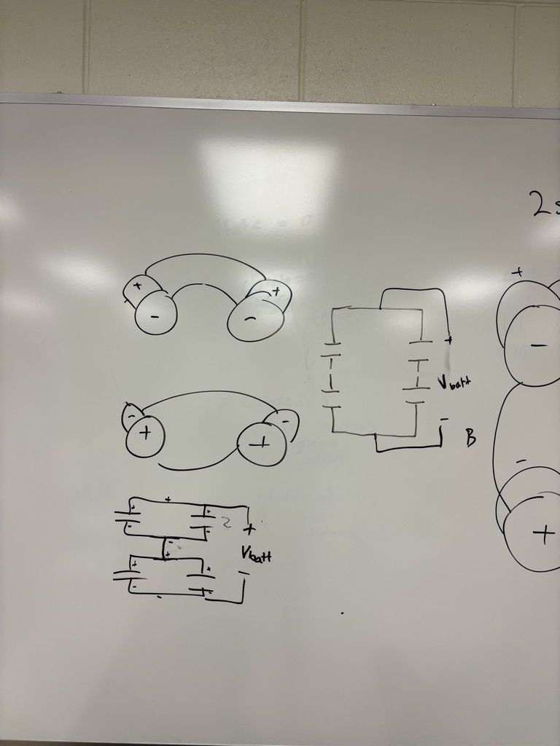
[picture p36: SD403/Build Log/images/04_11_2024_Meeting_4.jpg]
apr-11-2024-meeting-4

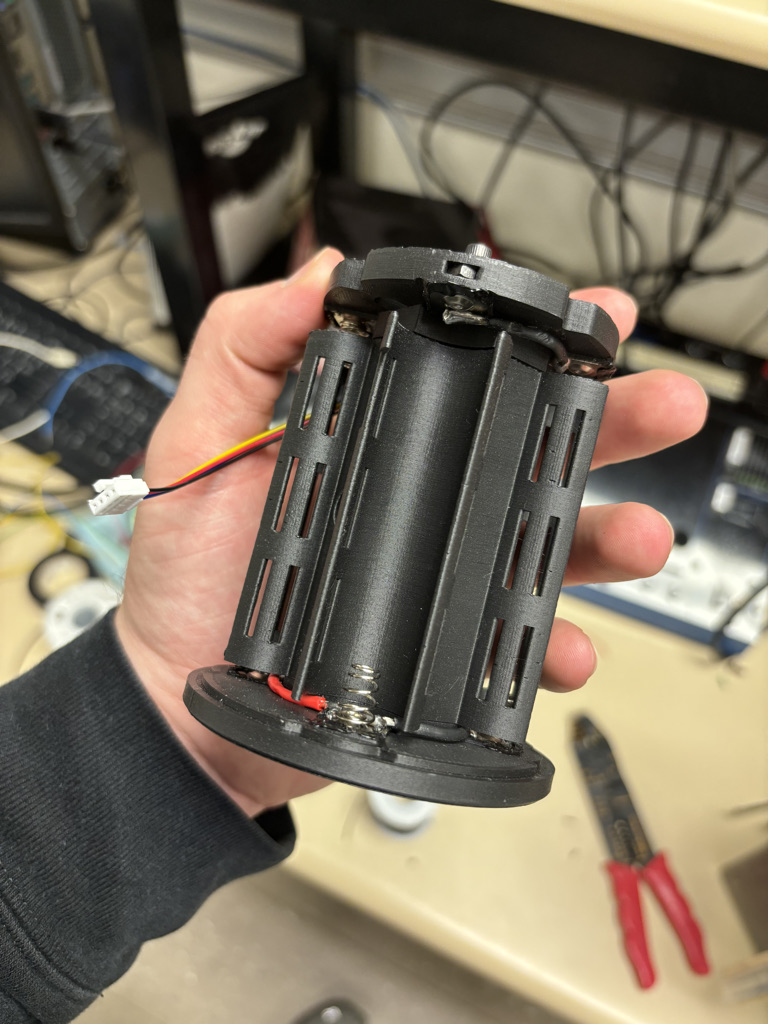
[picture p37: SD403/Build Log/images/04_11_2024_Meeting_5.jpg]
apr-11-2024-meeting-5


### Apr 18, 2024

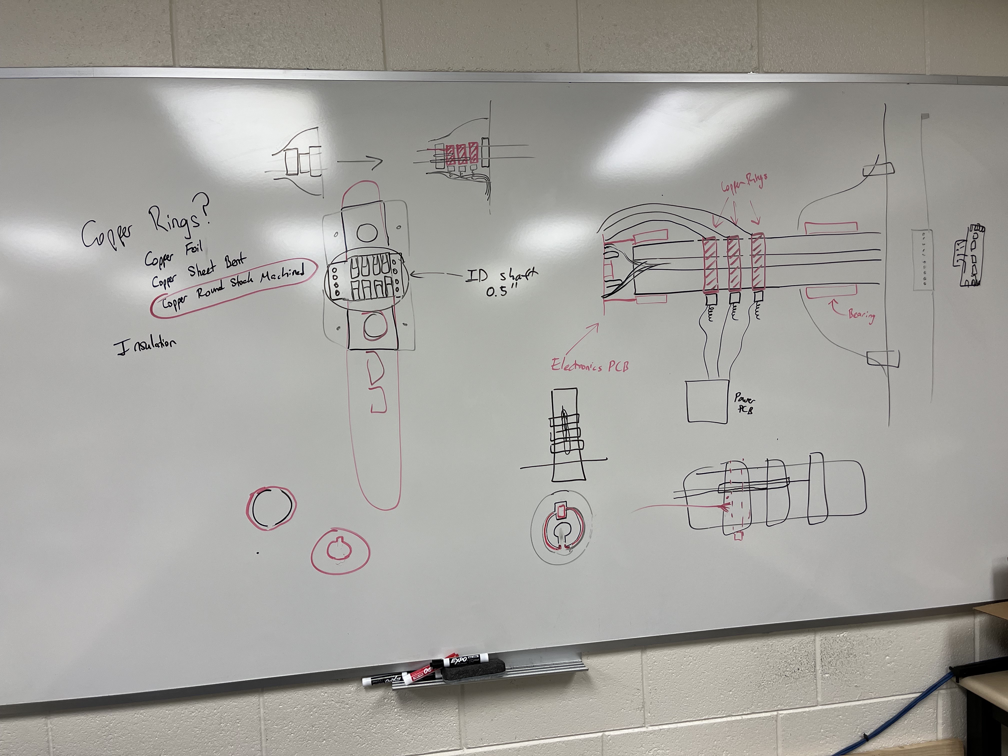
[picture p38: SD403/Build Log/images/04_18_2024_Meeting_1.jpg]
Apr-18-2024-meeting-1

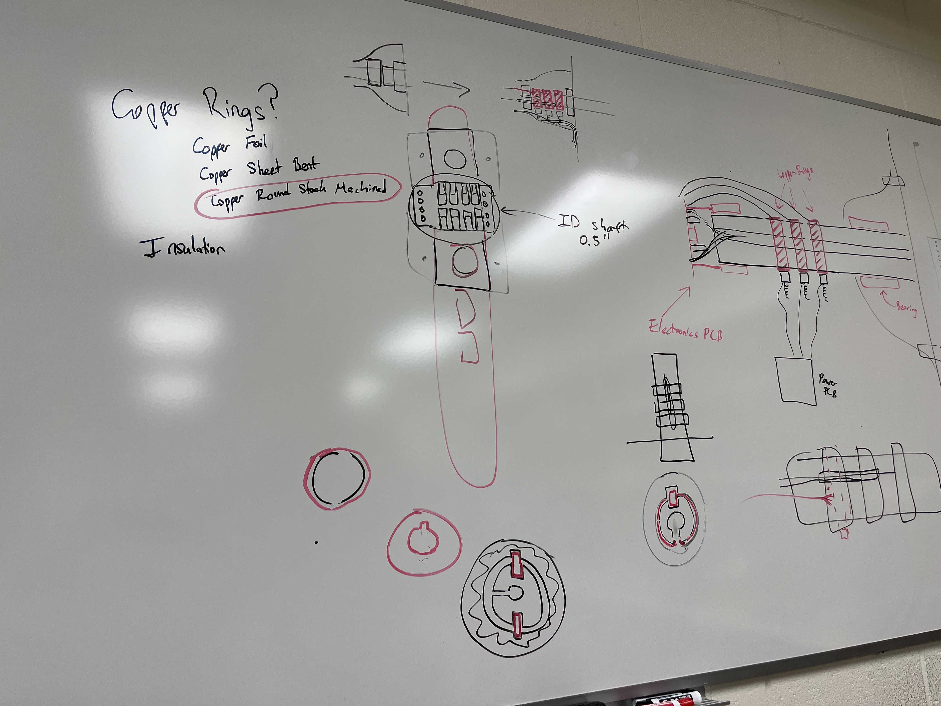
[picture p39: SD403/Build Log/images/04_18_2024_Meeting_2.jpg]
Apr-18-2024-meeting-2


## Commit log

2024-05-07 Migrated most of the oneDrive files over to the git repo
    [Electronics Enclosure - Core and Backplate only.3mf, Electronics Enclosure exterior.3mf, Electronics Enclosure interior.3mf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]
2024-05-08 Fixed a couple bugs and added LEDTest PlatformIO project
    [main.cpp]
2024-05-09 Made custom SPI driven LED library class and also added documentation for setting up the development environment.
2024-05-09 Fixed SPI_LED setStrip function
    [SPI_LED.cpp, main.cpp]
2024-05-11 Did a whole bunch of documentation for task 3 and also created the InterruptTest PlatformIO project
2024-05-11 Finished task 3 docs and implemented the LUT in C. also modified the matlab script to automatically generate a LUT according to the name of the image. Generated a plethora of LUTs.
    [LUT-DesertLandscape.csv, LUT-MATLAB-Symbol.csv, LUT-NDSU-football.csv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]
2024-12-18 Added new digital rpm sensor matlab script and restored a picture
